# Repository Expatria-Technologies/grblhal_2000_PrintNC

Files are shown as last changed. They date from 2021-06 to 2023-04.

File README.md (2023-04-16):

# GRBLHAL2000 for PrintNC EST

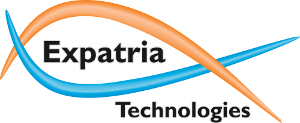
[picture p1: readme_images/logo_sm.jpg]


Expatria Technologies GRBLHAL Breakout board

Currently the successor to this board, the FlexiHAL is available available in our online store:

https://expatria.myshopify.com/products/flexi-hal

Please consider buying a board to support our open-source designs. 

grblHAL is a no-compromise, high performance, low cost alternative to parallel-port-based motion control for CNC milling, and the GRBLHAL2000 breakout board is a highly integrated, no compromise host platform for this awesome software.  Utilizing the high-performance PJRC Teensy 4.1 module, this board is designed to be a community driven project for the PrintNC, but useful for driving any type of CNC machine that uses external stepper drivers.

The GRBLHAL2000 was designed specifically for that machines that we are building in our lab, it is not intended to be everything to everyone.  The GRBL world is surprisingly vibrant and it is very likely that if we are missing a key feature for you, there are other designs out there that will be just what you are looking for.  But this board does include a few features that we couldn't find on other boards, and it reduces the amount of extra wiring in our setups.  In the co-operative spirit of the PrintNC community, and Open Source Hardware, the PNC HAL 2000 will be licensed and free to use by all parties, including commercial parties, under the CERN-OHL-P V2 license.  It is our hope that the community finds the design useful and that it may be carried forward to help advance the PrintNC and broader CNC hobby community.

Since this is not a commercial product, the best place to get a board (other than ordering a stack from the provided CAM files) is from the PrintNC community:
https://wiki.printnc.info/en/grbl/GRBLHAL2000-marketplace

The most recent A6 revision incorporates community driven updates from the PrintNC Electronic Standardization (EST) Project.  As part of this project, two additional breakout boards have been created for the user controls and limits/probe inputs.  These are simple boards and could easily be milled and hand assembled, but fabrication files for each are available in the CAM_Outputs folder.  In addition, the GRBLHAL2000 is intended to be used with the I2C jog controller or similar peripheral:

https://github.com/Expatria-Technologies/I2C_Jog_Controller

The key features of the GRBLHAL2000:

1) Integrated support for 3 wire powered switches such as the inductive type commonly used by the PrintNC community.
3) Onboard 5V regulator for the Teensy and PI connectors.
4) Integrated RS485 with automatic direction control.
5) Support for closed loop stepper motors and servos.
6) Differential interface for Spindle Sync inputs.
7) Sparkfun QWIIC differential I2C endpoint - extends the range of I2C and creates a robust data link for real-time jogging and control.  Note that due to chip availability issues, this interface has been replaced with pin headers on the A5 revision onwards.  See below for details.
8) Raspberry Pi GPIO connector allows integration of sender software and extended possibilities for network connectivity.

In addition, the board offers many of the same features found on other 32 bit GRBL controllers:

1) 5 axes of external step/direction for driving external stepper or servo drivers.
2) 10V or 5V spindle control.
3) 3 wire (powered) connections for standard GRBL buttons on breakout RJ45 connector.
4) XYZA limit switches and probe/toolsetter on breakout RJ45 connector.
5) Flood/mist relay drivers
6) Additional auxilliary inputs and relay driver outputs.

Optimized GRBLHAL driver is located here:
https://github.com/Expatria-Technologies/iMXRT1062/releases

## GRBLHAL2000 Overview

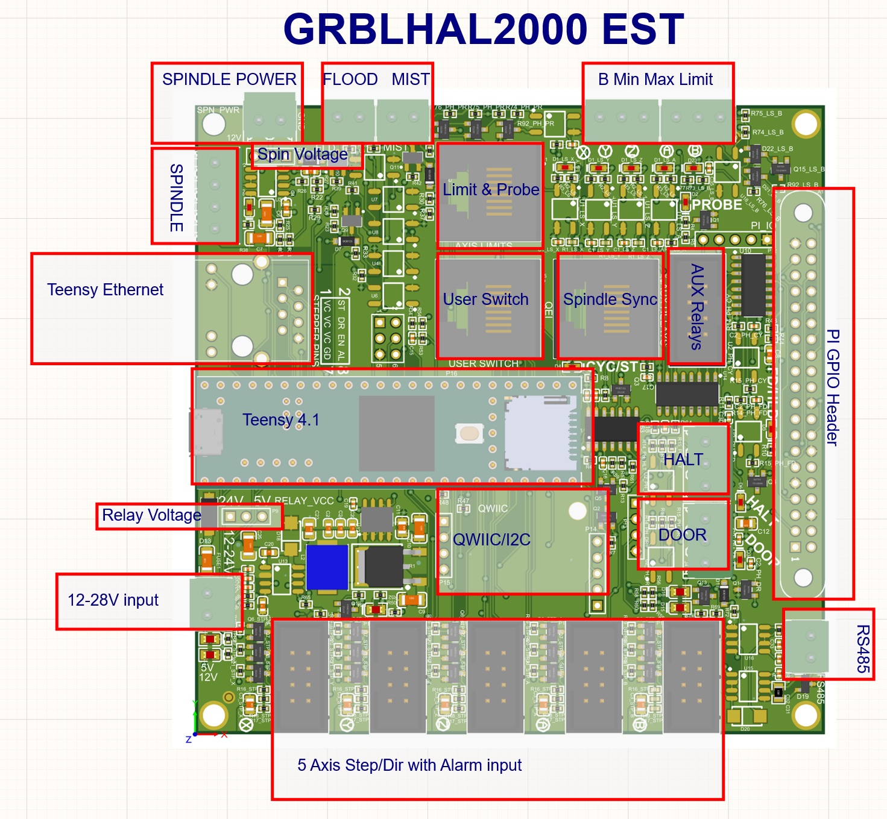
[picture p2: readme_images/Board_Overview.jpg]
Overview Image


### Teensy 4.1 Module
The GRBLHAL2000 uses the excellent Teensy4.1 port of GRBLHAL.  Both ethernet and USB-UART solutions can be used for sending g-code.  A UART is also connected to the PI header.

#### Soldering Instructions
The following pins need to be soldered between the GrblHAL2k and the Teensy: 
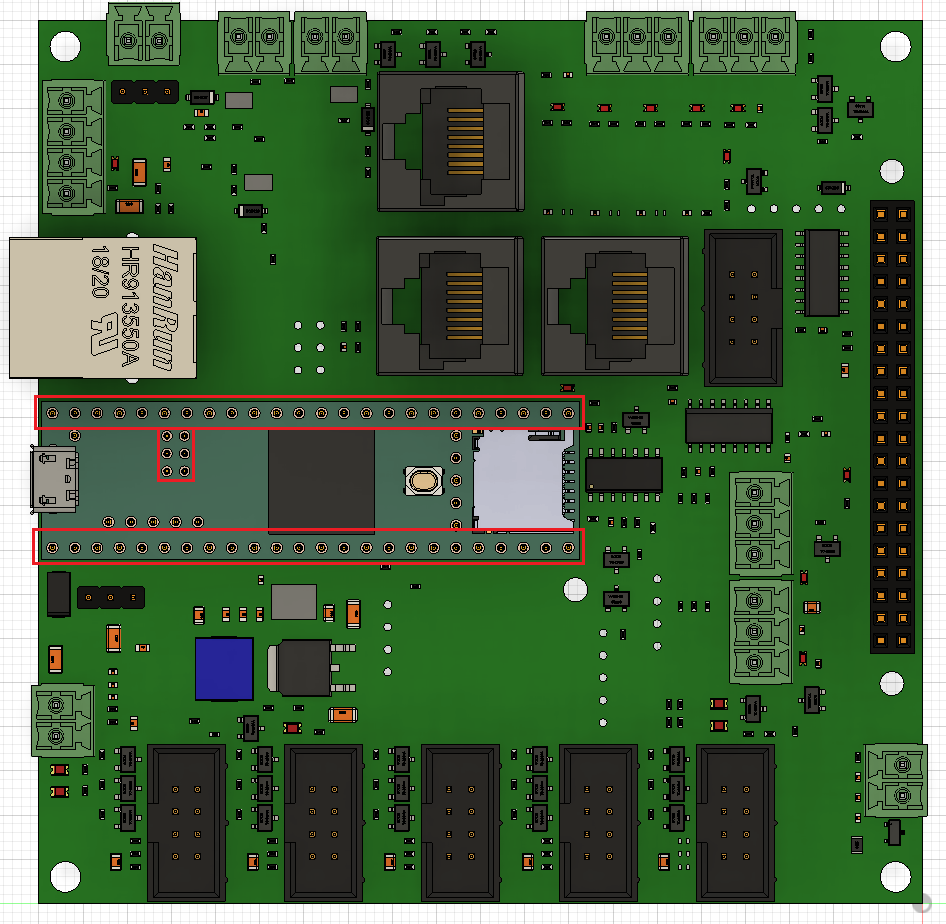
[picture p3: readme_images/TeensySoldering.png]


https://github.com/grblHAL/Plugin_networking/

### Power Input
There is a single input for 12-24VDC.  The board has its own onboard 5V regulator to power the Teensy module as well as a Pi Zero W (recommended) or Pi 3 A+ that is attached to the Pi GPIO header.  There is also a small capacity 12V LDO that is specifically for driving the limit and user switches, as well as optionally providing the base voltage for the 10V spindle output.  When driving the board with less than 14V input, it may not be possible to adjust the spindle output voltage to the full 10V.  In this case we recommend applying 12V to the external spindle supply input directly.

It is recommended that you cut the 5V power distribution trace on the Teensy 4.1.  This ensures that the USB power on the Teensy and the 5V regulator on the GRBLHAL2000 do not interact and create potential issues with back-powering.  Alternative solutions are detailed at pjrc:

https://www.pjrc.com/teensy/external_power.html

GRBLHAL2000 has reverse polarity as well as over-current protection beyond 1A.  This is important to consider when using external relays that draw a lot of current as this may overwhelm the capacity of the board.  If you need to drive more than 250 mA through the auxillary and mist/coolant relay outputs, external relays are likely required.

### Stepper Drivers
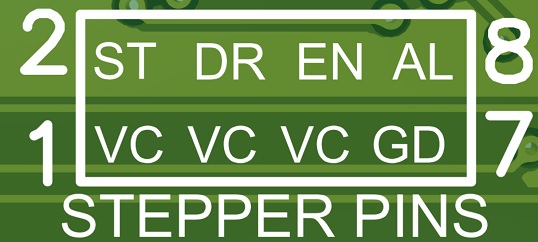
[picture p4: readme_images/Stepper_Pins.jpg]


The stepper drivers are designed to be used with IDC connectors that are quick to assemble.  Unfortuantely you will need to ensure that at the external driver the high and low signal pairs are connected correctly as there is no standard pinout on these drivers.  The 8 pin conneciton allows you to run a high and low pair for every signal to ensure the best possible signal integrity.  The board uses active low sinking outputs on the minus signal pins.  By default a common 5V is supplied to the plus pins.  If desired, L2 and L3 can be swapped so that the steppers can be driven with 12V.

### Analog Spindle Control
Traditional GRBL spindle control interface for 0-10V or 0-5V spindle control.  Uses a dual-stage output driver for linear response.  Spindle power supply is selectable between 5V, 12V or external.  Note that when running the board with less than 14v input, it may not be possible to reach the full 10V output level - this is due to the dropout of the 12V LDO.  In this case, use the external spindle power input to connect your 12v and bypass the LDO for the spindle control voltage.

On the bottom side of the Hal2k there is a solder bridge near the spindle section labelled PWM_CUT.  This jumper allows you to have a 12V compliant TTL PWM signal to drive a device like a laser engraver or an ESC.  Open the jumper for PWM output and close the jumper to output a continuous 0-10V analog signal.

### RS485 Spindle Control
This interface is primarily intended to be used with a Huanyang style VFD for spindle control.  The A and B pins are marked on the bottoms side of the PCB.  Simply connect the appropriate pins to the terminals on the VFD.  The auto-direction sensing circuit is modified from Bryan Varner's project:

https://github.com/bvarner/pi485

https://github.com/grblHAL/Plugins_spindle/

### 5 Axis limit inputs

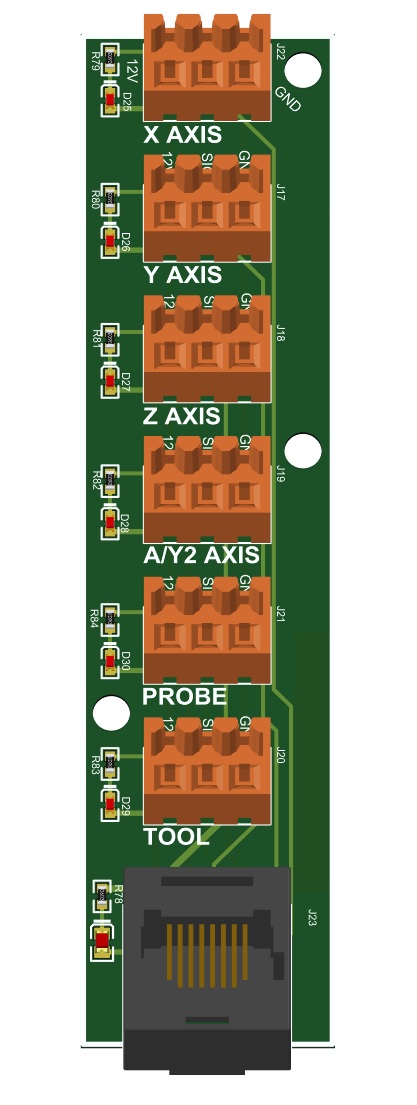
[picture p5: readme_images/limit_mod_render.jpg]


By default both GRBL and the GRBLHAL2000 expect NPN NC limit switches.  PNP switches are not supported. NO switches can also be used on any switch input

The first four axes have single limit inputs that are accessed via the RJ45 limit breakout connector.  A sample design for a breakout panel is included in the CAM_Outputs folder.  The fifth (M4 or B axis) limit input is multiplexed via XOR logic between two 3 wire connections to allow for future flexibility.  GRBL always knows the direction of travel so individual min and max pins are not required.  Auto-squaring is supported by enabling ganged axes in GRBLHAL and setting the appropriate pins.

In addition to the B limit, there are two probe input pins on the limit RJ45 breakout connector that are also multiplexed via XOR logic.

For both of the dual-input signals there is no need to terminate unused ports.

The RJ45 pinout:

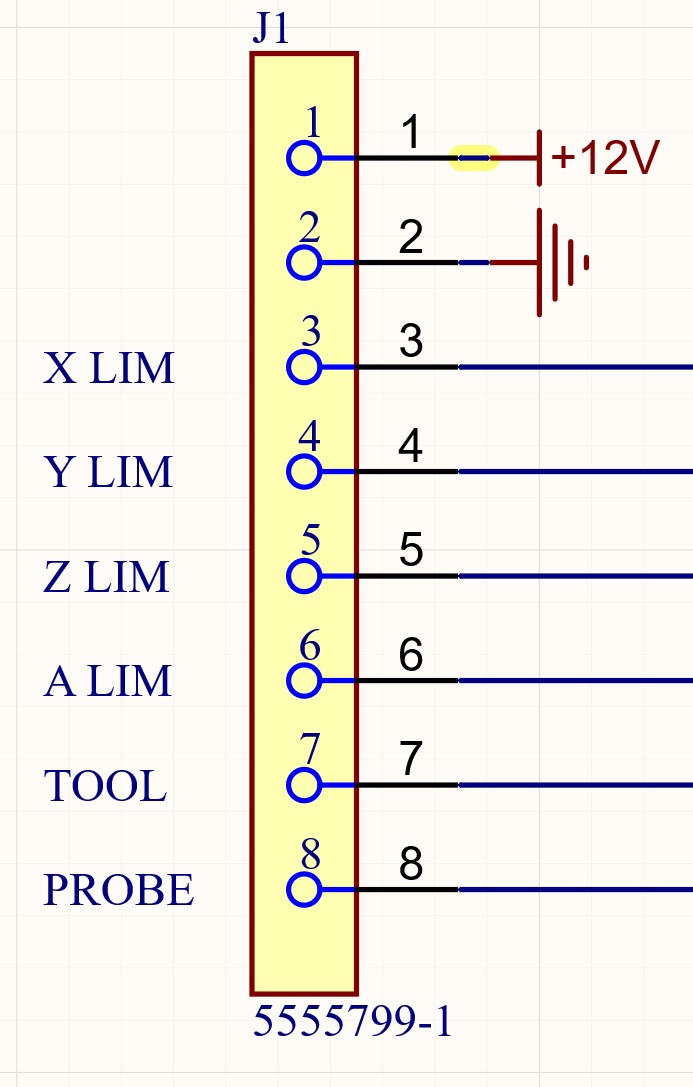
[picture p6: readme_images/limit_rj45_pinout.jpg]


### User Buttons
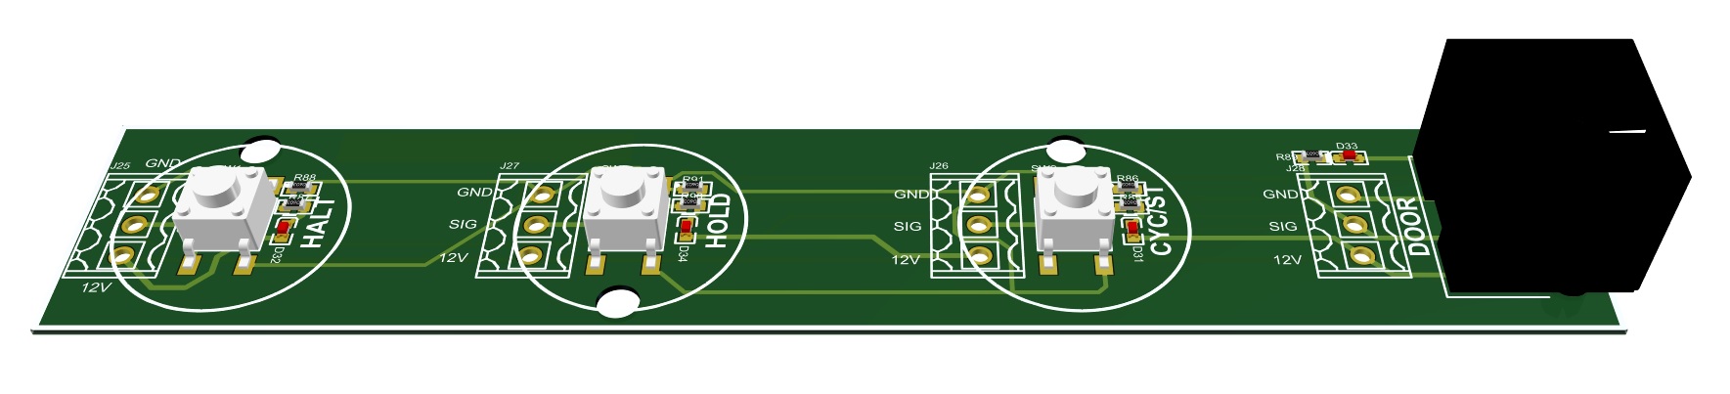
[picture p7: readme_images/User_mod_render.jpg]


Standard GRBL functions are mapped to 4 inputs.  These signals are primarily intended to be used via the user RJ45 connector.  For convenience, the HALT and DOOR signals are also exposed via 3 wire connections on the main PCB.  When multiplexed these signals must be NO logic.  A sample design for a button panel utilizing clear PETG buttons is included in the CAM_Outputs folder.

The RJ45 pinout:

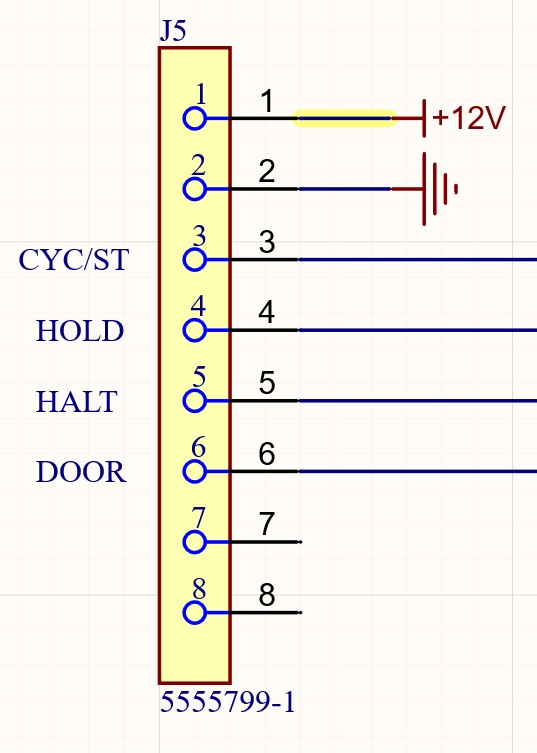
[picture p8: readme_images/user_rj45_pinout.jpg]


### Flood and Mist relay drivers - Auxillary relay drivers
The relay voltage is selectable between either the 12-24V input voltage, or the onboard 5V supply. P9 allows you to select the relay voltage.  If you need to drive more than 250 mA through the auxillary and mist/coolant relay outputs, larger external relays are likley required.

### Real-Time Control Port

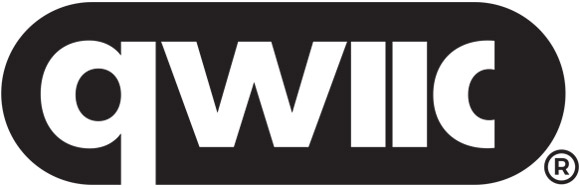
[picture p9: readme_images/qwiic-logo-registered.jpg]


On the A5 revision, this interface was revised to remove design dependence on the PCA9615 I2C extender chip.  Instead, pin headers are populated that expose all of the necessary signals to allow a custom I2C extender implementation.  In addition, a reference implementation using the PCA9615 is provided in the QWIIC_CARD folder to see how this might be accomplished and to allow interoperation with existing QWIIC pendants.

Please note that at least on Expatria designed pendants, the I2C interface module is usually included as a breakaway tab as part of the jogger pendant.  It will not be necessary to build the example QWIIC card separately.

This port is intended to allow for external pendant type devices to issue real-time jogging and override controls to the GRBLHAL controller.  It follows the QWIIC interface from Sparkfun, but adds additional signals for the keypad interrupt as well as the emergency stop.  We feel that a robust and wired control is the safest way to interact with a CNC machine in real time.  A simple reference controller implementation is under development, but there are some code examples referenced in the GRBLHAL I2C keypad plugin repository:

https://github.com/grblHAL/Plugin_I2C_keypad/

https://www.sparkfun.com/qwiic

### Spindle Sync Port
This port allows a differential connection to an external module for a robust GRBLHAL lathe implementation.  A reference encoder design is under development.  In addition solder jumper options are present to allow this connector to provide a quadrature encoder signal to the Teensy 4.1 QEI pins for future development.

### AUX Relay Port
Four axilliary relay outputs are exposed.  These have a maximum combined drive current of 500 mA.  The relay voltage can be selected via a 3 pin jumper between the external voltage input (12-28V) and the onboard 5V supply.  The 5V option cannot drive more than 20 mA per pin and is only used for TTL signalling applications - it should never be used to drive inductive loads.

### Raspberry PI expansion header

This is a standard Raspberry PI GPIO header.  The Pi has the ability to drive the axuilliary outputs, as well as read the status of the real-time control signals.  Three Pi GPIO signals are also brought out to a header on the top side of the board.  The GRBLHAL2000 is capable of powering a Pi Zero W or PI 3 A+ directly, but it cannot supply enough current for a full Pi 3 or Pi4 - when using those you must supply power to the PI externally.  Please note that A6 revision PCBA require a 90 degree headerwith the Pi mounted in a vertical orientation.

For communicating with the Teensy, the Pi can act as a standard g-code sender and send data over the connected UART.  The I2C keypad interface is also connected to allow for the potential to develop pi based real-time controls.  Finally, the Pi can assert the user switch controls such as emergency stop.  GRBL auxillary inputs are also routed to the Pi in the event they are unused by the GRBLHAL application.  The Pi can also be used to drive the auxilliar relay outputs.

### GRBLHAL2000 EST Ecosystem
Complete GRBLHAL2000 ecosystem with Jogger, breakouts and motion controller.

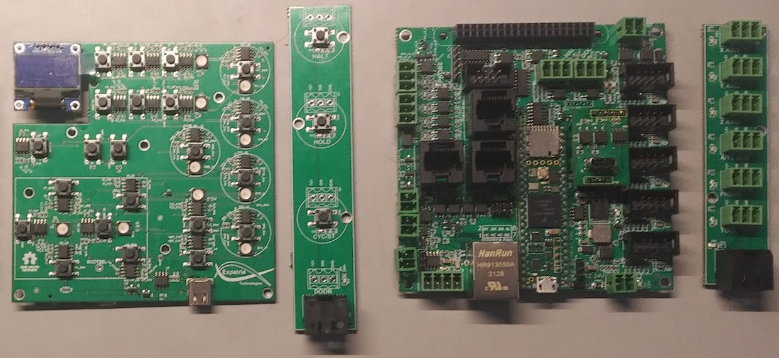
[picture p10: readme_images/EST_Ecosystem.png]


### Accessories

Some 3D printed accessories are avilable in [Mods & Accessories](https://github.com/Expatria-Technologies/Mods-Accessories/), including a mounting plate and enclosures/mounts for the limit and button breakouts.

### Attributions
This project uses components from the very helpful actiBMS library for JLCPCB SMT parts.

https://github.com/actiBMS/JLCSMT_LIB

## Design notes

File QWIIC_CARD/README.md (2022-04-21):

Please note that this design is for example only.  The I2C pendant designed by Expatria includes the necessary interface module.

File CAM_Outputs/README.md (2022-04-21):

# CAM Outputs

These folders contain the necessary files to upload to the fab and assembly service.

### GRBLHAL2000 Ecosystem


### GRBLHAL2000 Layer Ordering
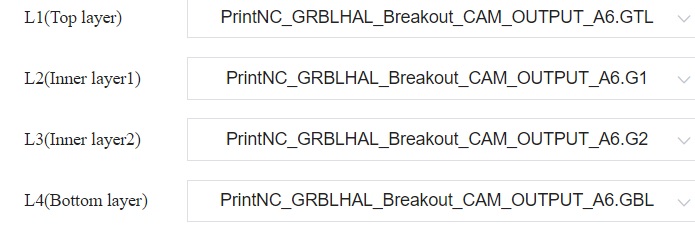
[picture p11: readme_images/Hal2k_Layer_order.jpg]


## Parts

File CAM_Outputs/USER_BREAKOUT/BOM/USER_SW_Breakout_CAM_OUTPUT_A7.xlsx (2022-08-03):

Comment | Description | Designator | Footprint | SuppliersPartNumber | Quantity
0603 Green | LED | D31 | 0603_LED_S1 | C72043 | 1
0603 Red | LED | D32 | 0603_LED_S1 | C2286 | 1
0603 Yellow | LED | D33, D34 | 0603_LED_S1 | C72038 | 2
RJHSE-5080 | CONN MOD JACK 8P8C R/A UNSHLD | J24 | FP-RJHSE-5080-MFG | C385834 | 1
AO3400A N | MOS(场效应管) | Q1, Q2, Q3 | SOT-23-3L | C700953 | 3
2KΩ ±1% | Chip resistor | R1, R2, R3, R85, R87, R89, R90 | 0603_R | C22975 | 7
K2-1102SP-C4SC-04 | Top Actuated 50mA @ 12VDC Round Button SPST 6*6mm Tactile Switches ROHS | SW1, SW2, SW3 | TECO-FSM4JSMATR_V | C127509 | 3

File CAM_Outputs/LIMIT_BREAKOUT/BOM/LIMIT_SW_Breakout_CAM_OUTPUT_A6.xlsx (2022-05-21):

Comment | Description | Designator | Footprint | SuppliersPartNumber | Quantity
0805 Green | LED | D24 | 0805_LED_S1 | C2297 | 1
0603 Yellow | LED | D25, D26, D27, D28 | 0603_LED_S1 | C72038 | 4
0603 White | LED | D29, D30 | 0603_LED_S1 | C2290 | 2
WJ15EDGVC-3.5-3P | Header,Male Pin,Covered(4 Sided) 3 1 0.138"（3.50mm） 3 P=3.5mm Pluggable System Terminal Block RoHS | J17, J18, J19, J20, J21, J22 | SL_3_50_180G_03 | C192778 | 6
424108314 | CONN MOD JACK 8P8C VERT UNSHLD | J23 | FP-5555799-1-MFG | C563815 | 1
10KΩ ±1% | Chip resistor | R78 | 0603_R | C25804 | 1
2KΩ ±1% | Chip resistor | R79, R80, R81, R82, R83, R84 | 0603_R | C22975 | 6

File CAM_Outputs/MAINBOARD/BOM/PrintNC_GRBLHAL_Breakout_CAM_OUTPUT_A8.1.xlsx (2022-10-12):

Comment | Description | Designator | Footprint | SuppliersPartNumber | Quantity
ADA3708 | Raspberry Pi Zero WH _Zero W with Headers_ | A1 | ADA3708_RPI-ZERO | C429949 | 1
100nF | Chip capacitors | C1_LS_A, C1_LS_X, C1_LS_Y, C1_LS_Z, C2_PH_CY, C2_PH_DR, C2_PH_FD, C2_PH_HLT, C13, C35_LS_B, C35_PH_PR | 0402_C | C1525 | 11
22uF | Chip capacitors | C3_STP_A, C3_STP_B, C3_STP_X, C3_STP_Y, C3_STP_Z, C11, C12, C23 | 0805_C | C602037 | 8
100nF | Chip capacitors | C4, C8, C20 | 0603_C | C14663 | 3
1uF | Chip capacitors | C5 | 0603_C | C15849 | 1
10uF | Chip capacitors | C6, C9, C10, C25 | 1206_C | C13585 | 4
100nF | Chip capacitors | C7 | 1206_C | C24497 | 1
1.0uF | Chip capacitor | C14, C19, C30, C31 | 0402_C | C52923 | 4
10nF | Chip capacitors | C15, C16, C17, C18, C26, C32, C33 | 0402_C | C15195 | 7
10uF | Chip capacitors | C21, C22, C24 | 0603_C | C19702 | 3
10pF | Chip capacitors | C27 | 0402_C | C32949 | 1
8.2nF | Chip capacitors | C28 | 0603_C | C27920 | 1
6.8nF | Chip capacitors | C29 | 0402_C | C1542 | 1
0603 Yellow | LED | D1_LS_A, D1_LS_X, D1_LS_Y, D1_LS_Z, D3, D5, D23 | 0603_LED_S1 | C72038 | 7
0603 White | LED | D2, D9 | 0603_LED_S1 | C2290 | 2
0603 Green | LED | D4 | 0603_LED_S1 | C72043 | 1
0603 Red | LED | D6 | 0603_LED_S1 | C2286 | 1
B5819W SL | Schottky Diode, 肖特基二极管 | D7, D8, D10, D17 | SOD-123 | C8598 | 4
0805 Green | LED | D11, D12, D16 | 0805_LED_S1 | C2297 | 3
SMAZ27-13-F | 27V ±5% 1W 500nA @ 20.5V SMA(DO-214AC) Zener Diodes RoHS | D13 | DIOM5226X240N | C155318 | 1
0805 Blue | LED | D14 | 0805_LED_S1 | C965817 | 1
0805 Red | LED | D15 | 0805_LED_S1 | C84256 | 1
SS54 | 二极管 | D18 | SMA(DO-214AC)_S1 | C22452 | 1
SM712 | Bidirectional 12V (Max), 7V (Max) 7.5V / 13.3V 10V / 20V 12A(8/20us) SOT-23-3 TVS RoHS | D19 | SOT95P230X117-3N | C293966 | 1
SS210 | 二极管 | D20 | SMA(DO-214AC)_S1 | C14996 | 1
BAV23C | 250V +150℃@(Tj) 350mW Dual Common Cathode 1.25V@200mA 50ns 100nA@250V 225mA SOT-23 Switching Diode ROHS | D21_LS_B, D21_PH_PR | SOT-23(SOT-23-3) | C545540 | 2
BAV23A | 250V +150℃@(Tj) 350mW 1 Pair Common Anode 1.25V@200mA 50ns 100nA@250V 225mA SOT-23 Switching Diode ROHS | D22_LS_B, D22_PH_PR | SOT-23(SOT-23-3) | C68976 | 2
24V 1A | 24V 1A 0.1s 1206 PTC Resettable Fuses RoHS | FUSE1 | 1206_C | C369160 | 1
424108314 | CONN MOD JACK 8P8C VERT UNSHLD | J1, J5, J16 | FP-5555799-1-MFG | C563815 | 3
 | 300V 8A 3 Straight pin 1 3.5mm Green Board Edge/Receptacle-Close P=3.5mm Pluggable System Terminal Block ROHS | J2, J3, J4, J6 | SL_3_50_180G_03 | C880555 | 4
 | OMNIMATE Signal - series BL/SL 3.50 | J8 | SL_SMT_3_5_180G_04 | C99845 | 1
0Ω ±1% | Chip resistor | L1, R31, R32, R36, R40, R43, R50 | 0402_R | C17168 | 7
33 uH | 33uH ±20% 2A 270mΩ SMD,6.6x7.3x3.0mm Power Inductors RoHS | L2 | INDPM7366X300N | C329385 | 1
C9135 | Male Box Header WR-BHD, THT, Vertical, pitch 2.54 mm, 8 pins | P1_STP_A, P1_STP_B, P1_STP_X, P1_STP_Y, P1_STP_Z, P6 | 61200821621 | C9135 | 6
Header 3 | Header, 3-Pin | P2, P9 | HDR1X3 | C49257 | 2
 | 300V 8A 2 Straight pin 1 3.5mm Green Board Edge/Receptacle-Close Straight,P=3.5mm Pluggable System Terminal Block ROHS | P3, P4, P5, P8, P11 | SL_3_50_180G_02 | C880554 | 5
Magjack | HR911105A Ethernet Interface Arduino Platform Evaluation Expansion Board | P7 | HANRUN_HR911105A | C163507 | 1
Header 3X2 | Header, 3-Pin, Dual row | P10 | HDR2X3 | C65114 | 1
Header 5 | Header, 5-Pin | P12, P14 | HDR1X5 | C124379 | 2
Header 4 | Header, 4-Pin | P15 | HDR1X4 | C124378 | 1
Header 6 2mm | Header, 6-Pin 2x3, 2mm pitch | P18 | HDR2X3 - 2mm | C225288 | 1
MMBT5551 G1 | 三极管 | Q1, Q2, Q3, Q4, Q5, Q6_STP_A, Q6_STP_B, Q6_STP_X, Q6_STP_Y, Q6_STP_Z, Q7_STP_A, Q7_STP_B, Q7_STP_X, Q7_STP_Y, Q7_STP_Z, Q8_STP_A, Q8_STP_B, Q8_STP_X, Q8_STP_Y, Q8_STP_Z, Q12, Q15_LS_B, Q15_PH_PR | SOT-23(SOT-23-3) | C2145 | 23
AO3400A N | MOS(场效应管) | Q9, Q10, Q11 | SOT-23-3L | C20917 | 3
MMBT5401 2L | 三极管 | Q13, Q14 | SOT-23(SOT-23-3) | C8326 | 2
10KΩ ±1% | Chip resistor | R1_LS_A, R1_LS_X, R1_LS_Y, R1_LS_Z, R22, R25, R28, R45, R49, R51, R65, R72, R73_LS_B, R73_PH_PR, R78, R79 | 0402_R | C25744 | 16
2KΩ ±1% | Chip resistor | R2_LS_A, R2_LS_X, R2_LS_Y, R2_LS_Z, R4, R6, R8, R10, R12, R46, R52, R67, R68, R74_LS_B, R74_PH_PR | 0402_R | C4109 | 15
4.7KΩ ±1% | Chip resistor | R3_LS_A, R3_LS_X, R3_LS_Y, R3_LS_Z, R14_PH_CY, R14_PH_DR, R14_PH_FD, R14_PH_HLT, R16_STP_A, R16_STP_B, R16_STP_X, R16_STP_Y, R16_STP_Z, R17_STP_A, R17_STP_B, R17_STP_X, R17_STP_Y, R17_STP_Z, R18_STP_A, R18_STP_B, R18_STP_X, R18_STP_Y, R18_STP_Z, R24, R26, R29, R33, R38, R47, R48, R55, R75_LS_B, R75_PH_PR, R76_LS_B, R76_PH_PR | 0402_R | C25900 | 35
51KΩ ±1% | Chip resistor | R5, R7, R9, R11, R13, R58, R60, R66 | 0402_R | C25794 | 8
1KΩ ±1% | Chip resistor | R15_PH_CY, R15_PH_DR, R15_PH_FD, R15_PH_HLT, R35, R39, R42 | 0402_R | C11702 | 7
2.2KΩ ±1% | Chip resistor | R19_STP_A, R19_STP_B, R19_STP_X, R19_STP_Y, R19_STP_Z, R20_STP_A, R20_STP_B, R20_STP_X, R20_STP_Y, R20_STP_Z, R21_STP_A, R21_STP_B, R21_STP_X, R21_STP_Y, R21_STP_Z | 0402_R | C25879 | 15
510Ω ±1% | Chip resistor | R23, R30, R34, R37, R41, R54, R59, R62, R64 | 0402_R | C25123 | 9
100KΩ ±1% | Chip resistor | R27, R53, R57, R61, R63 | 0402_R | C25741 | 5
5.6KΩ ±1% | Chip resistor | R56 | 0402_R | C25908 | 1
8.2KΩ ±1% | Chip resistor | R69 | 0402_R | C25924 | 1
120Ω ±1% | Chip resistor | R70 | 0805_R | C17437 | 1
3.9KΩ ±1% | Chip resistor | R71 | 0402_R | C51721 | 1
1.2KΩ ±1% | Chip resistor | R77 | 0402_R | C25862 | 1
47KΩ ±1% | Chip resistor | R92_LS_B, R92_PH_PR | 0402_R | C25792 | 2
EL357N(B)(TA)-G | 贴片光耦, Optocoupler SOP-4, EL357N(B)(TA)-G, Everlight Electronics | U1_LS_A, U1_LS_X, U1_LS_Y, U1_LS_Z, U2_PH_CY, U2_PH_DR, U2_PH_FD, U2_PH_HLT, U4, U5, U6, U7, U8, U18_LS_B, U18_PH_PR | SOP-4_P2.54 | C6649 | 15
LM358DR2G | LM358DR2G, Dual Op Amp, 5 - 28 V, 8-PinSOIC | U3 | SOIC-8_150mil | C7950 | 1
ULN2003AFWG | 大电流驱动 | U10 | SOIC-16_150mil | C5437 | 1
74HC14D | 74系列逻辑芯片 | U11 | SOIC-14_150mil | C5605 | 1
24LC16BT-I/SN | IC EEPROM 16KBIT I2C 8SOIC | U12 | SOIC-SN8_L | C6480 | 1
TPS54331DR | DC-DC芯片 | U13 | SOIC-8_150mil | C9865 | 1
AM26LS32ACDRG4 | 接口芯片 | U14 | SOIC-16_150mil | C6180 | 1
SN75176BDR | RS-485/RS-422 | U15 | SOIC-8_150mil | C7063 | 1
NE555DR |  | U16 | SOIC-8_150mil | C7593 | 1
L78M12ABDT-TR | DNI | VR1 | TO-252-2-180 | C61534 | 1

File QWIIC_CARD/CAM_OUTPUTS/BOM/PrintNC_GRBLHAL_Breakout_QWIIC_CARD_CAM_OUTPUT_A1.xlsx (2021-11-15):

Comment | Description | Designator | Footprint | SuppliersPartNumber | Quantity
1.0uF | Chip capacitor | C1, C3 | 0402_C | C52923 | 2
100nF | Chip capacitors | C2, C4 | 0402_C | C1525 | 2
5555799-1 | CONN MOD JACK 8P8C VERT UNSHLD | J1 | FP-5555799-1-MFG | C305983 | 1
Header 5 | Header, 5-Pin | P18 | HDR1X5 | C124379 | 1
Header 4 | Header, 4-Pin | P19 | HDR1X4 | C124378 | 1
470Ω ±1% | Chip resistor | R1, R5, R6, R8 | 0402_R | C25117 | 4
100Ω ±1% | Chip resistor | R2, R7 | 0402_R | C25076 | 2
680Ω ±1% | Chip resistor | R9, R11 | 0402_R | C25130 | 2
10KΩ ±1% | Chip resistor | R10 | 0402_R | C25744 | 1
PCA9615DPJ DNI | IC REDRIVER I2C 2CH 10TSSOP | U1 | FP-SOT552-1-IPC_C | C2652385 | 1
EL357N(B)(TA)-G | 贴片光耦 | U2, U3 | SOP-4_P2.54 | C6649 | 2

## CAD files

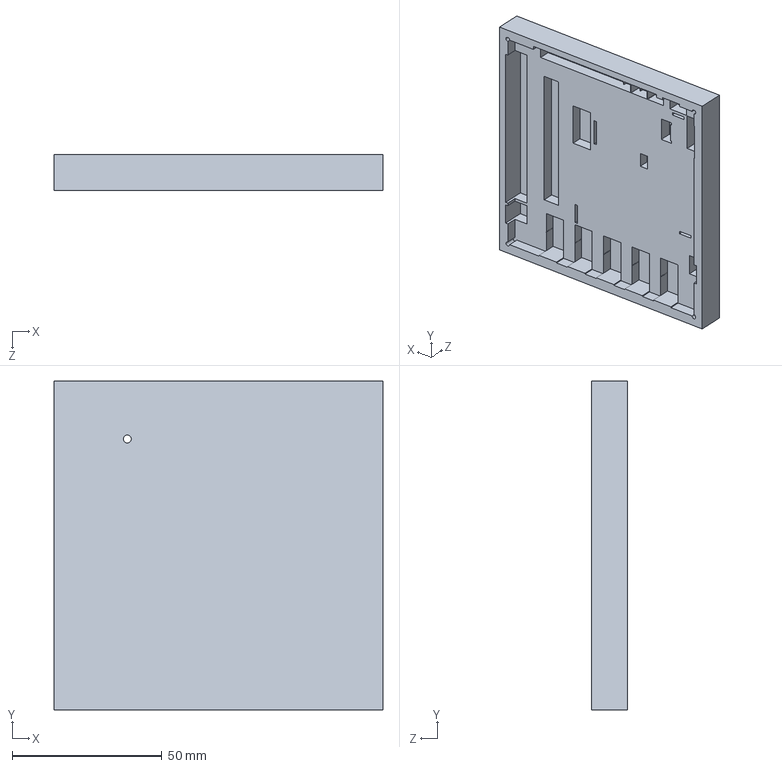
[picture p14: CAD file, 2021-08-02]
Assembly_Jig/holder_plate.SLDPRT
110.0 x 110.0 x 12.0 mm

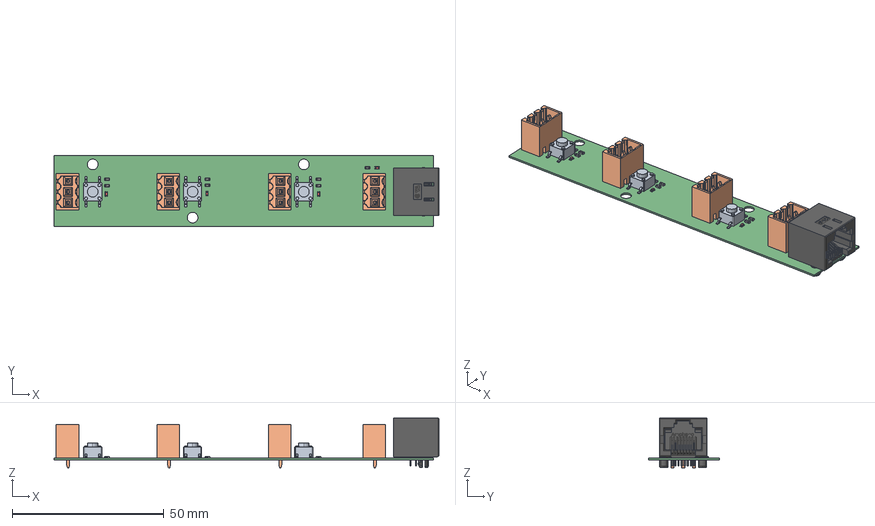
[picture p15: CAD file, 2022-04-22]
STEP_EXPORT/USER_SW_Breakout.step
126.7 x 23.5 x 16.4 mm
Conn_Amphenol_RJHSE-5080_eec
c-4-1437565-2-s-3d x 3
User_Library-RES_1609-0603 x 7
SL_3.50_03_180G_3.2SN_OR_BX_1604480000 x 4
User_Library-LED_0603_R_Pocket002 x 4
User_Library-LED_0603_R_Pad004 x 4
User_Library-LED_0603_R_Fillet x 4
User_Library-LED_0603_R_Pocket001 x 4
User_Library-LED_0603_R_Pad x 4

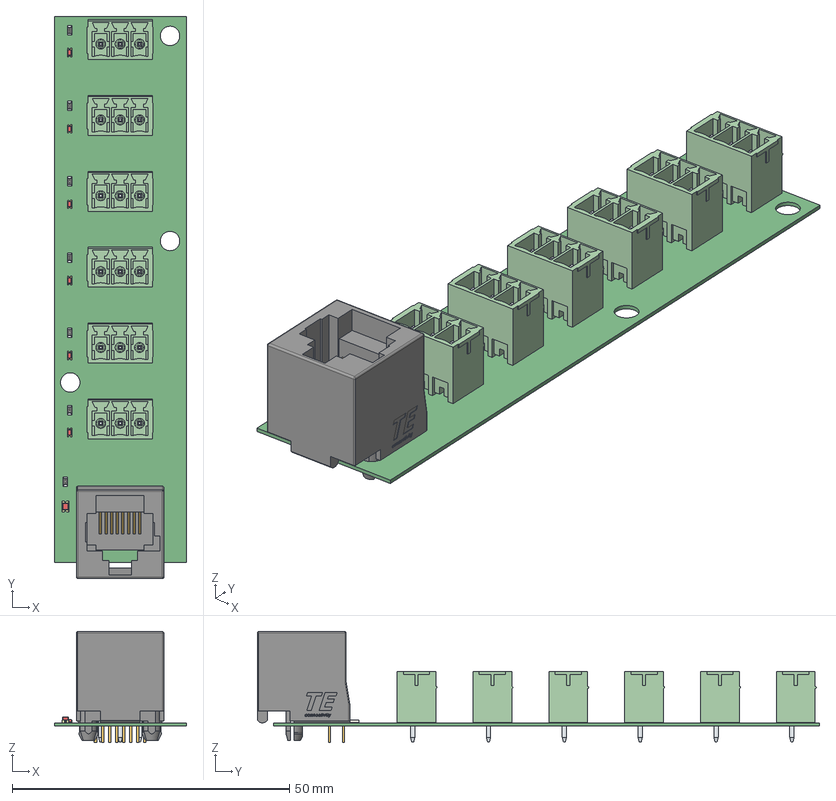
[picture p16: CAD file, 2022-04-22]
STEP_EXPORT/LIMIT_SW_Breakout.step
23.9 x 101.4 x 20.1 mm
plastic
pins_
User_Library-RES_1609-0603 x 7
6913211000xx_PIN x 18
User_Library-LED_0603_R_Pocket002 x 6
User_Library-LED_0603_R_Pad004 x 6
User_Library-LED_0603_R_Fillet x 6
User_Library-LED_0603_R_Pocket001 x 6
User_Library-LED_0603_R_Pad x 6
User_Library-led_0805

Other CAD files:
Assembly_Jig/holder_plate.STL

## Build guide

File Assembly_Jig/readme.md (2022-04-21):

This assembly jig is provided for reference only.  It is not compatible with the EST revisions.

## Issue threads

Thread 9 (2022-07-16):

Regarding sn75176 IO levels

muhammadelmogy, 2022-07-16:
I see that you are using the sn75176 IC for RS485 interface and feeding the IC with 5V!
According to the datasheet, minimum Vcc is  4.75V and you are feeding the comm lines(SDA, SCL) directly to the Teensy!
From what I know the [Teensy4.1 pins is 3.3V tolerance not 5v tolerance ](https://github.com/TeensyUser/doc/wiki/Teensy-Compatibility)unless I am wrong, can you explain this issue?
Shouldn't you be using some kind of voltage translator ?

andrewmarles, 2022-07-17:
Yes, it is a 5V part.  VCC range is 4.75 to 5.25V so the 5V supply is completely correct.  The minimum input voltage for logic high is 2V so there is no problem feeding the TX from teensy into this part at 3.3V.

In the RX direction, there is a voltage divider (R68, R69) so that the maximum voltage seen at the teensy is ~3.1V, again this is well above the minimum logic high level of the teensy and there is no 5V logic at the teensy pins.

No discrete translator is required.

muhammadelmogy, 2022-07-17:
I do not know how did I fail to notice this voltage divider, but in that case wouldn't that affect the rise time of the signal, I am wondering what is the max safe baud rate in that case?

andrewmarles, 2022-07-17:
No issues with 115200 if the vfd supports it.

Closed 2022-07-17.

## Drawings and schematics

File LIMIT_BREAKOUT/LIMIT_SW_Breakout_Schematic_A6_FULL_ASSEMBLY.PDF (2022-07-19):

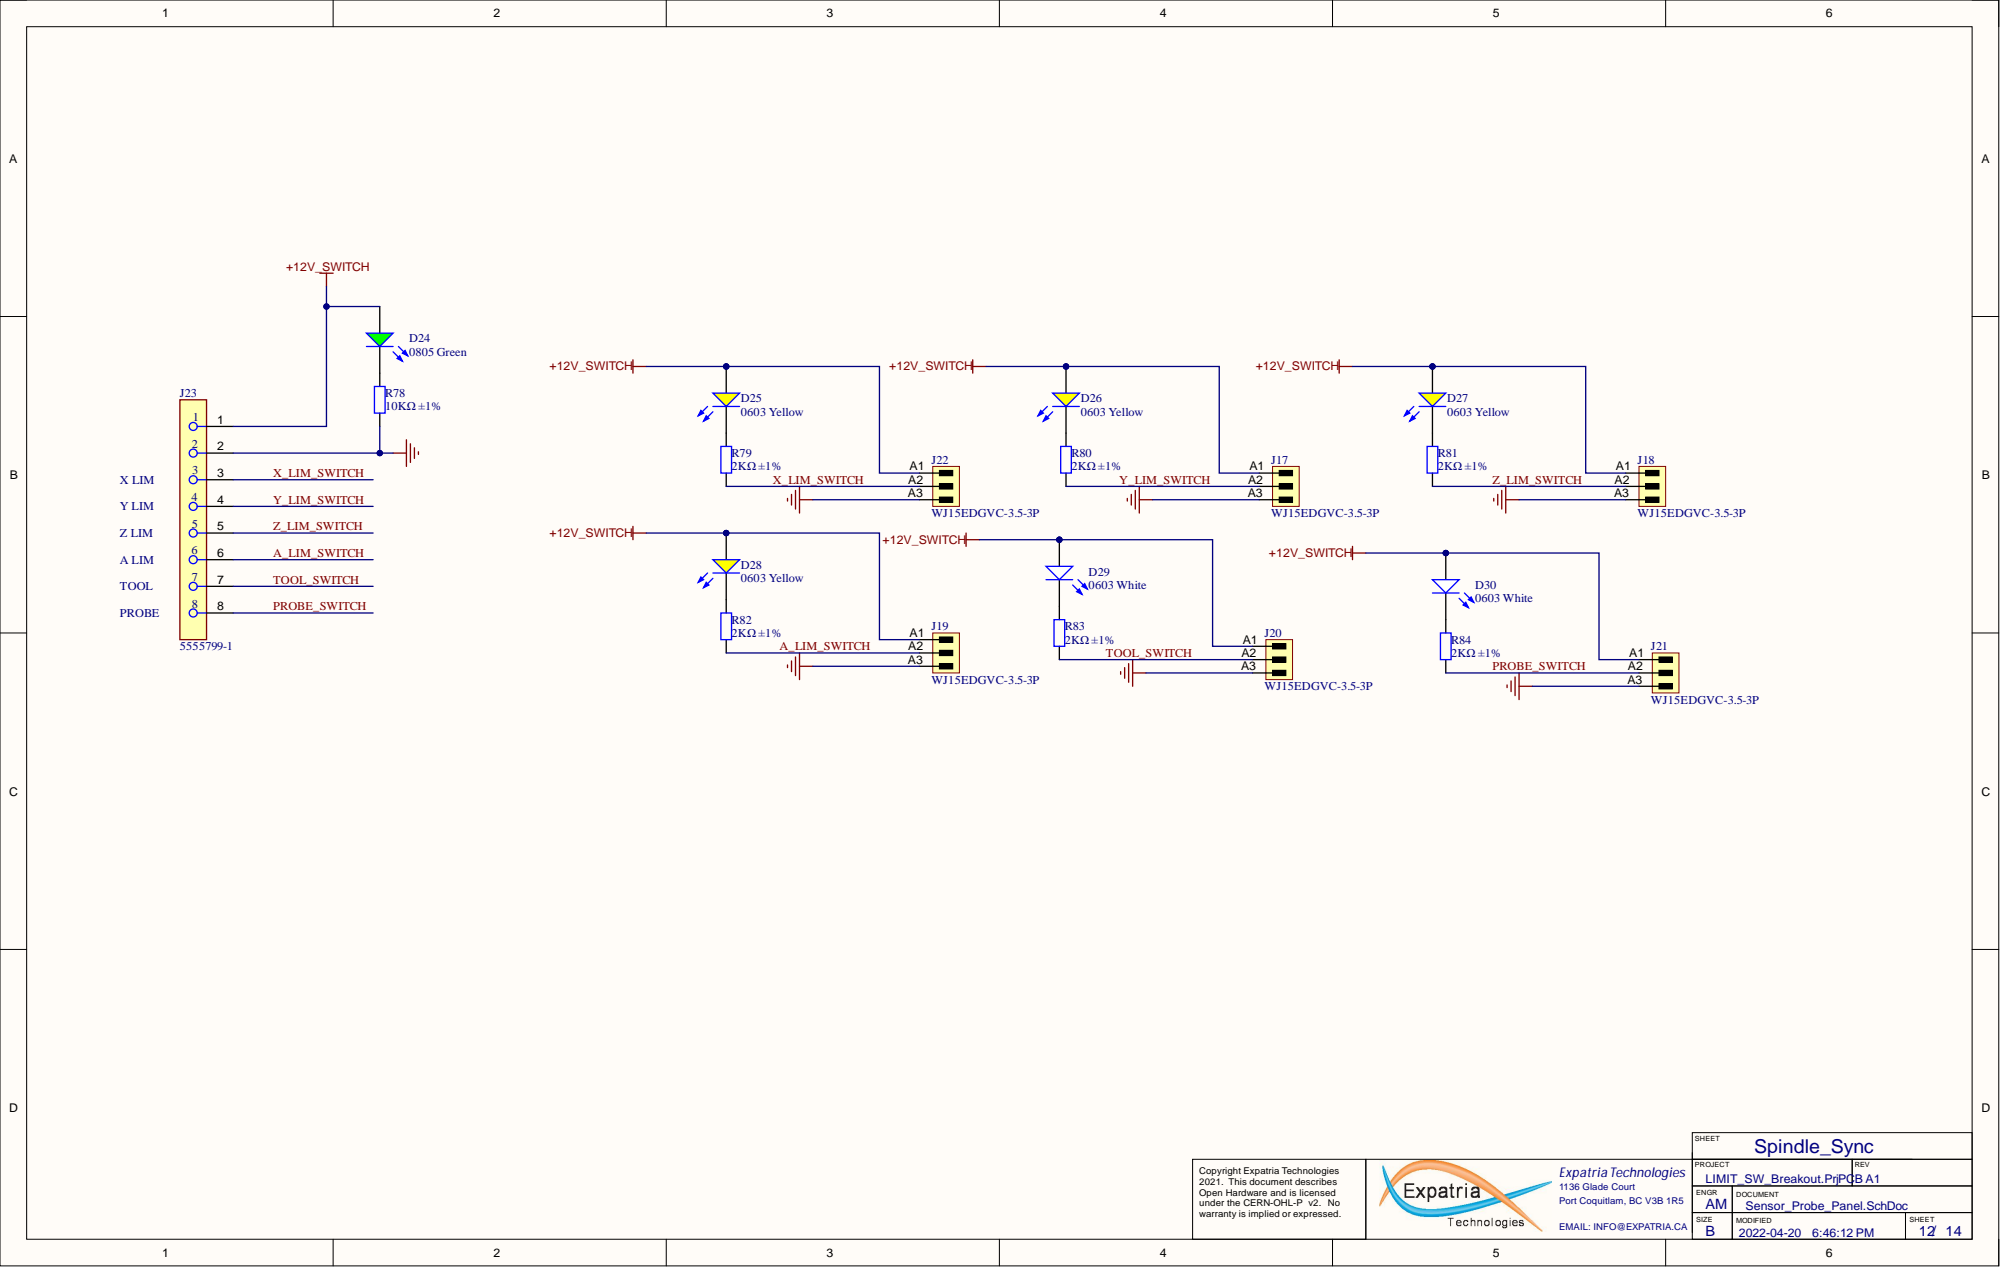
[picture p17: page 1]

X LIM Y LIM Z LIM A LIM TOOL

A3 | | PROBE _SWIT C H A2

Co p yri g ht Ex p atri a Te c h n o l o g i e s 2 0 2 1. Th i s d o c u m e nt d e s cri b e s O p e n Hardware a n d i s l i c e n s e d u n d er th e CERN-OHL-P v 2. No warra nty i s i m p l i e d or e x pre s s e d . | | P R OJE C T LI M I T_SW_Breakout . P rj P C | R E V B A1

E N G R A M | D O C U M E N T Sensor_Probe_Panel.Sc h D o c

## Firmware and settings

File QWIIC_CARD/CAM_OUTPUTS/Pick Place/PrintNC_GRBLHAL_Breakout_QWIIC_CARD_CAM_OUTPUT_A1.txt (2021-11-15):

Altium Designer Pick and Place Locations
C:\Repo\grblhal_2000_PrintNC\QWIIC_CARD\Project Outputs for PrintNC_GRBLHAL_Breakout_QWIIC_CARD\PrintNC_GRBLHAL_Breakout_QWIIC_CARD_UPLOAD_GERBERS_A1\Pick Place\PrintNC_GRBLHAL_Breakout_QWIIC_CARD_CAM_OUTPUT_A1.txt

========================================================================================================================
File Design Information:

Date:       12-10-21
Time:       11:43
Revision:   Not in VersionControl
Variant:    FULL_ASSEMBLY
Units used: mil

Designator Comment          Layer    Footprint         Center-X(mil) Center-Y(mil) Rotation Description                      
U2         EL357N(B)(TA)-G  TopLayer SOP-4_P2.54       1176.181      187.992       270      ????                             
U1         "PCA9615DPJ DNI" TopLayer FP-SOT552-1-IPC_C 875.984       364.173       270      "IC REDRIVER I2C 2CH 10TSSOP"    
U3         EL357N(B)(TA)-G  TopLayer SOP-4_P2.54       1176.181      600.394       270      ????                             
R6         "470O ±1%"       TopLayer 0402_R            826.772       610.236       90       "Chip resistor"                  
R8         "470O ±1%"       TopLayer 0402_R            821.851       88.583        270      "Chip resistor"                  
R7         "100O ±1%"       TopLayer 0402_R            930.118       182.087       90       "Chip resistor"                  
R10        "10KO ±1%"       TopLayer 0402_R            1058.071      602.362       90       "Chip resistor"                  
R1         "470O ±1%"       TopLayer 0402_R            821.851       182.087       270      "Chip resistor"                  
R9         "680O ±1%"       TopLayer 0402_R            1131.890      384.843       0        "Chip resistor"                  
R2         "100O ±1%"       TopLayer 0402_R            826.772       524.606       90       "Chip resistor"                  
R11        "680O ±1%"       TopLayer 0402_R            1218.504      384.842       0        "Chip resistor"                  
R5         "470O ±1%"       TopLayer 0402_R            875.984       182.087       90       "Chip resistor"                  
J1         5555799-1        TopLayer FP-5555799-1-MFG  563.779       377.559       270      "CONN MOD JACK 8P8C VERT UNSHLD" 
C1         1.0uF            TopLayer 0402_C            935.039       608.268       270      "Chip capacitor"                 
C4         100nF            TopLayer 0402_C            875.984       88.583        90       "Chip capacitors"                
C2         100nF            TopLayer 0402_C            880.905       608.268       270      "Chip capacitors"                
C3         1.0uF            TopLayer 0402_C            930.118       88.583        90       "Chip capacitor"                 
P19        "Header 4"       TopLayer HDR1X4            68.898        448.622       270      "Header, 4-Pin"                  
P18        "Header 5"       TopLayer HDR1X5            1028.543      272.244       90       "Header, 5-Pin"                  

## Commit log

2021-06-11 Commit A1 schematic PDF.
2021-06-18 Commit A2 design files, schematic pdf and readme images.
    [2xparallelswitch.SchDoc, 5V_Power_Supply.SchDoc, Change Log.SchDoc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]
2021-06-18 Commit board photo.
2021-06-22 Updated spindle control 0-10V. Updated step alarm. Removed PWM spindle option. Updated component values.
    [Change Log.SchDoc, Misc_switches.SchDoc, Photocoupler12Vinput.SchDoc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]
2021-08-02 Commit A4 design and GERBER files.
    [2xparallelswitch.SchDoc, Change Log.SchDoc, I2C_Keypad.SchDoc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]
2021-08-02 Updated Stepper_Pins.jpg
2021-08-09 Fixed issue with D22 orientation.
    [PrintNC_GRBLHAL_Breakout_CAM_OUTPUT_A4.csv]
2021-10-07 Commit WIP A5 changes ahead of removing QWIIC.
    [PrintNC_CNC_Breakout.SchDoc, PrintNC_GRBLHAL_Breakout.PrjPCB, RS485.SchDoc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]
2021-10-12 Commit A5 revisions: Delete QWIIC and add headeers Update BOM for availability Revised to new magjack connector
    [2xparallelswitch.SchDoc, 5V_Power_Supply.SchDoc, I2C_Keypad.SchDoc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]
2021-11-15 Commit A5 files and remove A4
    [JLPCB BOM-PrintNC_GRBLHAL_Breakout_A4_SMT_ONLY.xlsx, JLPCB BOM-PrintNC_GRBLHAL_Breakout_A5_FULL_ASSEMBLY.xlsx, JLPCB BOM-PrintNC_GRBLHAL_Breakout_A5_SMT_ONLY.x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]
2021-11-15 Commit QWIIC PCA9615 interface module example.
    [I2C_Keypad.SchDoc, PrintNC_GRBLHAL_Breakout_QWIIC_CARD.PrjPCB, PrintNC_GRBLHAL_Breakout_QWIIC_CARD.pcbdoc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]
2022-02-22 Initial commit of A6 changes for EST.
    [2xparallelswitch.SchDoc, 5V_Power_Supply.SchDoc, I2C_Keypad.SchDoc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]
2022-02-27 Commit revisions ahead of breaking off breakoffs.
    [PrintNC_CNC_Breakout.SchDoc, PrintNC_GRBLHAL_Breakout.PrjPCB, PrintNC_GRBLHAL_Breakout.SCHLIB]
2022-04-21 Commit new and revised board files.
    [1x_limit_switch.SchDoc, 2xparallelswitch.SchDoc, LIMIT_SW_Breakout.PrjPCB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]
2022-04-21 Commit manufacturing files.
    [JLPCB BOM-PrintNC_GRBLHAL_Breakout_A5_FULL_ASSEMBLY.xlsx, JLPCB BOM-PrintNC_GRBLHAL_Breakout_A5_SMT_ONLY.xlsx, LIMIT_SW_Breakout_CAM_OUTPUT_A6.csv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]
2022-04-21 Commit readme images.
    [Limit_Switches.SchDoc, Misc_switches.SchDoc, USER_SW_Breakout.pcbdoc]
2022-04-21 Remove pin headers from button panel.
    [USER_SW_Breakout_CAM_OUTPUT_A6.xlsx]
2022-04-21 Commit minor fixes.
    [LIMIT_SW_Breakout.pcbdoc, USER_SW_Breakout_CAM_OUTPUT_A6.xlsx, User_Button_Panel.SchDoc]
2022-04-22 Remove pi header from BOM.
    [PrintNC_GRBLHAL_Breakout_CAM_OUTPUT_A6.xlsx]
2022-04-22 Remove A6 files.
    [PrintNC_GRBLHAL_Breakout_CAM_OUTPUT_A6.csv, PrintNC_GRBLHAL_Breakout_CAM_OUTPUT_A6.xlsx]
2022-04-22 Commit A7 files and step models.
    Only change was rotated Pi header.
    [LIMIT_SW_Breakout.PrjPCB, LIMIT_SW_Breakout.pcbdoc, LIMIT_SW_Breakout.step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]
2022-04-23 Updated TVS in BOM.
    [LIMIT_SW_Breakout.pcbdoc, PrintNC_GRBLHAL_Breakout_CAM_OUTPUT_A7.xlsx]
2022-04-23 Removed teensy headers due to the fact it is hard to find teensy4.1 without headers.
    [PrintNC_CNC_Breakout.SchDoc, PrintNC_GRBLHAL_Breakout_CAM_OUTPUT_A7.xlsx]
2022-05-21 substituted RJ45 jack.
    [LIMIT_SW_Breakout_CAM_OUTPUT_A6.xlsx, PrintNC_GRBLHAL_Breakout_CAM_OUTPUT_A7.txt, PrintNC_GRBLHAL_Breakout_CAM_OUTPUT_A7.xlsx]
2022-07-19 Update user breakout BOM to address LED forward voltage variation.
    [USER_SW_Breakout_CAM_OUTPUT_A6.xlsx]
2022-07-19 Adjusted component values on switch board and RS485 bias.
    [Limit_Switches.SchDoc, Misc_switches.SchDoc, PrintNC_GRBLHAL_Breakout.PrjPCB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]
2022-07-19 Commit latest schematic pdf.
2022-07-19 Commit project files.
    [PrintNC_GRBLHAL_Breakout.PrjPCB, USER_SW_Breakout.PrjPCB]
2022-07-28 Optimized component placement around RS485. Fixed issue with 5V power.
    [PrintNC_GRBLHAL_Breakout.PrjPCB, PrintNC_GRBLHAL_Breakout_CAM_OUTPUT_A8.1.csv, PrintNC_GRBLHAL_Breakout_CAM_OUTPUT_A8.1.xlsx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]
2022-08-03 Commit updated A7 user switch breakout.
    [USER_SW_Breakout.PrjPCB, USER_SW_Breakout.pcbdoc, USER_SW_Breakout_CAM_OUTPUT_A6.1.xlsx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]
2022-08-05 Changing 3 components.
    This is done mainly to adjust for out of stock components, but also to change a 22µF capacitor that is not used anymore in JLCPCB.
    Changelog :
    - Cap 22µF : from C45783 to C602037
    - Diode : from C328584 to C68976
    - 3 pin connector : from C192778 to C880555
    [PrintNC_GRBLHAL_Breakout_CAM_OUTPUT_A8.1.xlsx]
2022-09-03 Changing two components in the BOM.
    Changing a led as the previous one was flagged as "standard" assembly, which is more costly.
    Also, changing the 2 pin connector to be from the same company than the 3 pin one and select the same male pins.
    - switching led C2293 to C965817
    - swiching 2-pin straight receptactle from C192777 to C880554
    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
    [PrintNC_GRBLHAL_Breakout_CAM_OUTPUT_A8.1.xlsx]
2022-09-14 added f3d and
    [Button Breakout Case v2.step, Button PCB Case Bottom.stl, Button PCB Case Cover.stl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]
2022-10-12 Commit latest schematic.
2022-10-24 Add case & mount for limit breakout PCB
    [Limit Breakout Case Base.stl, Limit Breakout Case Lid.stl, Limit Breakout Lightpipe x7.stl]
2023-01-22 Remove 3D-Prints, which have been migrated to Mods & Accessories
    [Button Breakout Case v2.step, Button PCB Case Bottom.stl, Button PCB Case Cover.stl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]
